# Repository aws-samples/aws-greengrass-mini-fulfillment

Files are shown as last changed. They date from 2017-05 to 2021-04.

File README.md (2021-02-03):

## The Greengrass mini-fulfillment center example 

At re:Invent 2016 AWS Greengrass was introduced to the world. This miniature 
fulfillment center demonstration was used to display what could be done with 
Greengrass when announced. It has since been upgraded to use the publicly available 
version of [Greengrass](https://aws.amazon.com/greengrass/) v1.
 
A [video](https://youtu.be/XQQjX8GTEko?t=27m27s) was taken of the completed and 
operational Greengrass-based miniature fulfillment center, a.k.a. "dual robot arm demo" 
in action at re:Invent. Since re:Invent this demo and example has continued to 
evolve. It has been the seed for [other demos](https://youtu.be/dpatdO2uPCA) and 
now supports Greengrass [discovery](http://docs.aws.amazon.com/greengrass/latest/developerguide/gg-discover-api.html) 
capabilities. 

The artifacts, example code, and instructions to construct this demo are 
available in this repository as an example. We look forward to seeing what 
you'll do with it.

#### Directory Structure and Noteworthy Files
```
aws-greengrass-mini-fulfillment/
  +- docs/
  |  +- BOM.md         -- the bill of materials necessary for construction
  |  +- CONSTR.md      -- instructions for physical construction (TODO)
  |  +- INSTALL.md     -- instructions for software provisioning and install
  |  +- OPERATE.md     -- instructions for operation of the demo
  |  +- TIDBITS.md     -- tiny pieces of setup information that might be helpful
  |  +- TROUBLE.md     -- troubleshooting of install and operation
  |
  +- groups/
  |  +- cert_setup.py  -- generates local certificates used by Greengrass groups 
  |  +- group_setup.py -- provisions and deploys example Greengrass groups 
  |  +- servo_setup.py -- prepares the servo communication code for example use  
  |  |
  |  +- arm/           -- the code and config necessary for an arm host
  |  |  +- ggd/        -- the Greengrass Devices that will be run on the Host
  |  |  |  +- servo/   -- the servo communications libraries 
  |  |  +- inv_arm/    -- the specific config and certs for the `inv_arm` group 
  |  |  +- sort_arm/   -- the specific config and certs for the `sort_arm` group
  |  | 
  |  +- lambda/        -- the Lambda functions used in the Greengrass groups
  |  |
  |  +- master/        -- the directory of the `master` Greengrass group 
  |     +- certs/      -- the group AWS IoT and local certs to be copied to Core
  |     +- ggd/        -- the Greengrass Devices that will be run on the Host
  |        +- certs/   -- the client certs used by GG devices
  |        +- flask/   -- where the web GG device gets files to serve
  |        +- servo/   -- the servo communications libraries 
  |
  +- models/           -- the models used to 3D print components of this demo
  +- LICENSE
  +- README.md -- this file
  +- requirements.txt
```

After following the [installation instructions](docs/INSTALL.md), each directory 
contains all the files necessary to support one of the three Demo groups' hosts. 
There are three Greengrass Groups named: 

| Group | Host Name | Description |
| :---: | :---: | :--- |
| `inv_arm` | `inv_arm-pi` | contains the Inventory Arm devices and the Inventory Arm Core |
| `master` | `master-pi` | contains both the Conveyor Belt devices and the Master Core |
| `sort_arm` | `sort_arm-pi` | contains the Sorting Arm devices and the Sort Arm Core |

The demo behavior is broken into the concept of a series of simple control stages 
organized by Group. Those stages are:

| Group | Control Stages |
| :--- | :--- |
| **Inventory Arm** | `... > Home > Finding > Pickup > Shipping > Home > ...` |
| **Master** | `..conveyor direction..` |
| **Sorting Arm** | `... > Home > Finding > Pickup > Sorting > Home > ...` |

As shown in the video above, even with these simple stages the interaction between 
the three Groups displays complex, cohesive, and coordinated behaviors.

This is possible because the whole system is modeled as a collection of micro-services. 
Those micro-services then leverage high-speed local messaging to enable communication 
within and between groups, as well as transactional state control using local device 
shadows. 

The high-level, local architecture of the demo is:
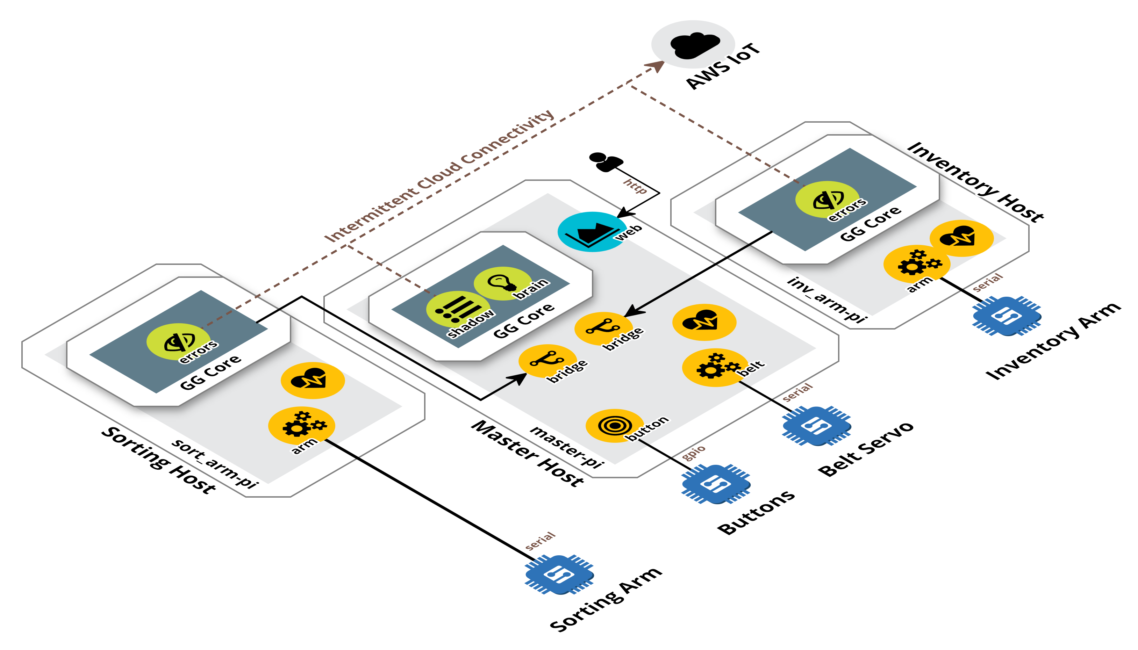
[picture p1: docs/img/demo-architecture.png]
mini-fulfillment demo architecture


#### Master/Conveyor Host
There are six processes on this host:
- the Master Greengrass Core
- the [`heartbeat`](groups/master/ggd/heartbeat.py) Greengrass Device (GGD) process
- the [`bridge`](groups/master/ggd/bridge.py) GGD process
- the [`belt`](groups/master/ggd/belt.py) GGD process -- manages the conveyor belt servo
- the [`button`](groups/master/ggd/button.py) GGD process -- manages the button box's red, green, and white control buttons
- the [`web`](groups/master/ggd/web.py) GGD process

Within the Master Core, these are the Lambda functions:
- [`MasterErrorDetector`](groups/lambda/MasterErrorDetector/error_detector.py) -- this function monitors local telemetry and detects any error states
- [`MasterBrain`](groups/lambda/MasterBrain/master_brain.py) -- this function monitors the fabric of telemetry coming from the 
  bridges and the local GGDs. This function will decide what to do with respect 
  to current telemetry and errors in the system

There is a web visualization on this host. If one browses to: `<master_ip>:5000` a 
visualization that reads data from the Master Core can be seen. 

#### Inventory Arm Host
There are three processes on this host:
- the Inventory Arm Greengrass Core
- the [`heartbeat`](groups/arm/ggd/heartbeat.py) Greengrass Device (GGD) process
- the [`arm`](groups/arm/ggd/arm.py) GGD process

Within the Inventory Arm Core, this is the Lambda function:
- [`ArmErrorDetector`](groups/lambda/ArmErrorDetector/error_detector.py) -- this function monitors local telemetry and detects any error states

#### Sorting Arm Host
There are three processes on this host:
- the Sorting Arm Greengrass Core
- the [`heartbeat`](groups/arm/ggd/heartbeat.py) Greengrass Device (GGD) process
- the [`arm`](groups/arm/ggd/arm.py) GGD process

Within the Sort Arm Core, this is the Lambda function:
- [`ArmErrorDetector`](groups/lambda/ArmErrorDetector/error_detector.py) -- this function monitors local telemetry and detects any error states

#### Noteworthy Files
There are some noteworthy files in the repository that centralize a fair amount 
of work around the instantiation of this demonstration.
- `groups/group_setup.py` – performs all provisioning of each host's Greengrass Group. 
This file has commands that are useful when instantiating this demo and that demonstrate the use of the Greengrass REST APIs.
    - `create <group_type> <config_file>` – creates a Greengrass Group for a given 
    group type and configuration file. Also stores all of the provisioning 
    artifacts (i.e. `GroupID`, `CoreDefinitionId`, etc.) in the local configuration file.
    - `deploy <config_file>` – deploys a previously provisioned Greengrass Group
    - `clean-all <config_file>` – cleans up the entirety of a Greengrass Group 
    and the locally stored provisioning artifacts.
- `groups/servo_setup.py` – prepares the servo manufacturer's communication library 
for use on a Raspberry Pi with the Raspbian OS.

## DIY
If you'd like to build a copy of this demo yourself you'll want to read both 
the [installation instructions](docs/INSTALL.md) and the 
[construction instructions](docs/CONSTR.md). Please share any feedback you have 
or questions you run into here as [Issues](https://github.com/awslabs/aws-greengrass-mini-fulfillment/issues).

## Special Thanks
[Brett Francis](https://github.com/brettf) and [Todd Varland](https://github.com/toddvarland) would like to thank the following. Without their 
help and existence we simply would not have made this demo.

> **The Francis Family, The Varland Family, [gg-group-setup](https://github.com/awslabs/aws-greengrass-group-setup), 
[ROBOTIS](https://github.com/ROBOTIS-GIT/DynamixelSDK), [Servode](https://github.com/brettf/servode), 
Pretty Lights, Sigur Ros, Flume - Insanity, Amazon.com, HBO Silicon Valley, The [Greengrass](https://aws.amazon.com/greengrass/) Developers**

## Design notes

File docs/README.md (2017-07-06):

#### ToC

| File | Description |
| :--- | :--- |
| `BOM.md` | the bill of materials necessary for construction|
| `CONSTR.md` | instructions for physical construction |
| `INSTALL.md` | instructions for software installation and example provisioning |
| `OPERATE.md` | instructions for operation of the example |
| `TIDBITS.md` | tiny pieces of setup information that might be helpful |
| `TROUBLE.md` | troubleshooting of install and operation |

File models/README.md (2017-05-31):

The 3d printing files for the robot arms.

`TODO: assembly instructions`

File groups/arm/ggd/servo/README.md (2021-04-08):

# Servode
An ode to Python code that uses Servos ([ROBOTIS](https://github.com/ROBOTIS-GIT/DynamixelSDK) first)

## Usage
### As a library
When using Servode as a library use a single ServoProtocol instance per 
connected servo bus. One ServoProtocol can be shared across threads.

To connect a Servo and read a register (example: `present_position`):
```python
with ServoProtocol() as sp:
    servo = Servo(sp=sp, servo_id=1)
    # to read a value
    value = servo['present_position']
```

To connect a Servo and write a register (example: `goal_position`):
```python
with ServoProtocol() as sp:
    servo = Servo(sp=sp, servo_id=1)
    # to read a value
    servo['goal_position'] = 128
```

To connect a group of servos and write values to a register (example: `goal_position`):
```python
with ServoProtocol() as sp:
    sg = ServoGroup()
    sg['base'] = Servo(sp, 10)
    sg['elbow'] = Servo(sp, 11)
    sg['wrist'] = Servo(sp, 12),
    sg['claw'] = Servo(sp, 13)

   sg.write("goal_position", [
        100,  # first servo value
        200,  # second servo value
        330,  # third servo value
        400   # fourth servo value
    ])
```

### From the command-line
To read a register from one servo:
```
$ ./servode.py read_register --sid 10
2016-11-04 06:01:42,582|servode |INFO: Read register: 'present_position'
2016-11-04 06:01:42,587|servode |INFO: Servo:10 value:497
```
To read a register from two servos:
```
$ ./servode.py read_register --sid 10 --sid 11
2016-11-04 06:01:42,582|servode |INFO: Read register: 'present_position'
2016-11-04 06:01:42,587|servode |INFO: Servo:10 value:497
2016-11-04 06:01:42,589|servode |INFO: Servo:11 value:102
```
To write a value to a register on one servo:
```
$ ./servode.py write_register goal_position 490 --sid 10
2016-11-04 06:23:28,716|servode |INFO: Servo:10 wrote value:490 to register:goal_position
```
To write a value to a register on two servos:
```
$ ./servode.py write_register goal_position 490 --sid 10 --sid 11
2016-11-04 06:24:11,614|servode |INFO: Servo:10 wrote value:490 to register:goal_position
2016-11-04 06:24:11,616|servode |INFO: Servo:11 wrote value:490 to register:goal_position
```
## Installation

1. Download the latest [ROBOTIS SDK](https://github.com/ROBOTIS-GIT/DynamixelSDK/releases)
2. Change to the directory where `servode.py` resides
3. Un-tar the ROBOTIS SDK:

    ```
    #example
    tar -xvf ~/download/dir/of/DynamixelSDK-#.#.#.tar
    ```  
4. Copy the dynamixel python functions to the directory where `servode.py` resides

    ```
    # example
    cp DynamixelSDK-#.#.#.tar/python/dynamixel_functions_py/dynamixel_functions.py .
     ```
5. Edit `dynamixel_functions.py` to use the CDLL for your OS. 
    - Example CDLL edit for Raspbian Jessie: 
    ```python
        ...snip...
        from ctypes import cdll
        # dxl_lib = cdll.LoadLibrary("../../c/build/win32/output/dxl_x86_c.dll") # for windows 32bit
        # dxl_lib = cdll.LoadLibrary("../../c/build/win64/output/dxl_x64_c.dll") # for windows 64bit
        # dxl_lib = cdll.LoadLibrary("../../c/build/linux32/libdxl_x86_c.so")    # for linux 32bit
        # dxl_lib = cdll.LoadLibrary("../../c/build/linux64/libdxl_x64_c.so")    # for linux 64bit
        dxl_lib = cdll.LoadLibrary("DynamixelSDK-3.4.1/c/build/linux_sbc/libdxl_sbc_c.so")    # for linux 32bit sbc
        ...snip...

    ```

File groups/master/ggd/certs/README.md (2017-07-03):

All the Greengrass Device specific certificates and keys land here

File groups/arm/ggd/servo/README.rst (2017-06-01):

Servode
=======
An ode to Python code that uses Servos (ROBOTIS first)

`Getting Started <https://github.com/brettf/servode>`_

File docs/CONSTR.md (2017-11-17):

# AWS Mini Fulfillment Center Construction

Welcome to the AWS Mini Fulfillment Construction Documentation. 

## Construction Instructions

Overall the process is:
1) acquire parts from the [Bill of Materials](BOM.md)
1) print 3D parts
1) assemble each [arm](#the-arm)
1) assemble [control box](#the-control-box)
1) assemble [conveyor](#the-conveyor)
1) follow [software installation](INSTALL.md)
1) push green button

## The Arm
The quickest way to assemble the various parts that form a complete robot arm is 
to assemble them in four separate sections and combine them at the intersection 
points. The arm's four main sections are in this image:

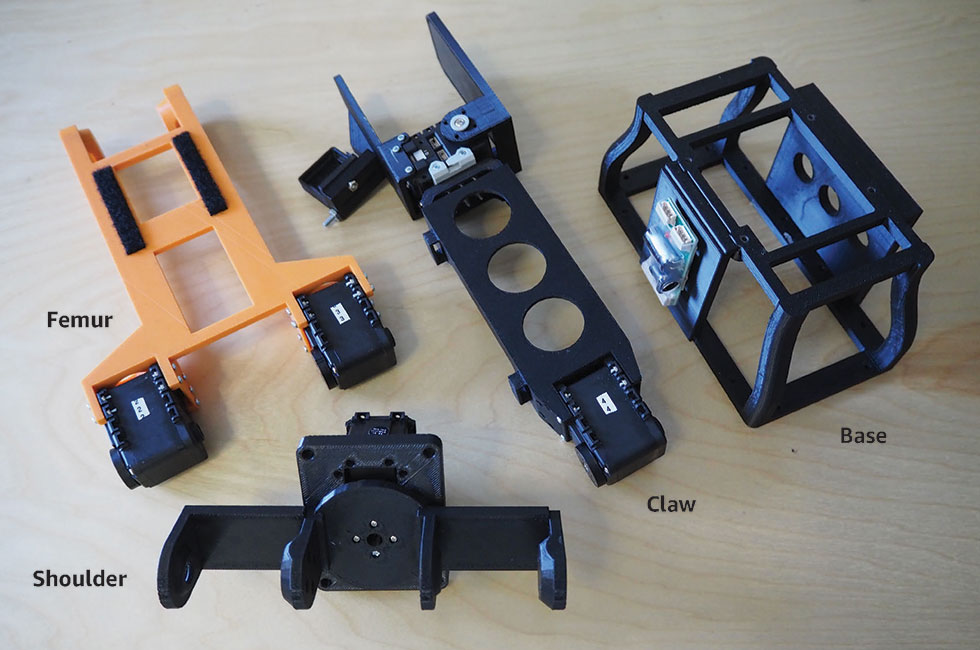
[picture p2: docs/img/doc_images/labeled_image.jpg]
four main parts


### The Shoulder

| Image | Instructions | 
| :--- | :--- |
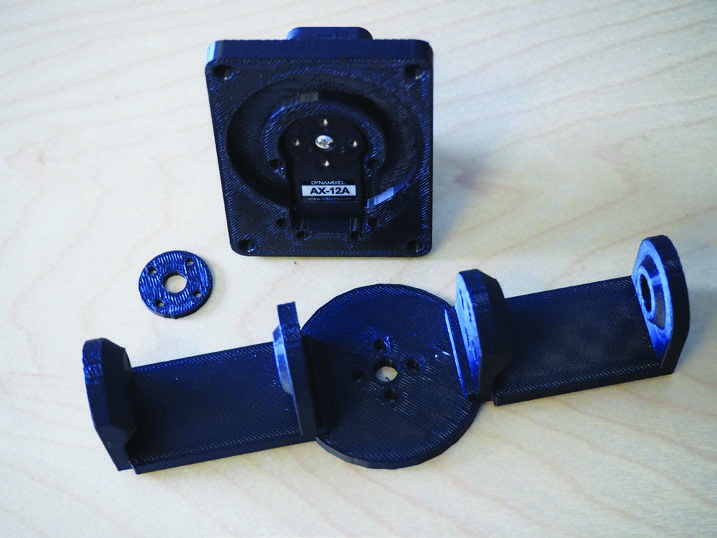
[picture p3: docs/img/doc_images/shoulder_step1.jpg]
|  | Connect the Servo to the large square spacer using six N1 bolts and six S3 screws. |
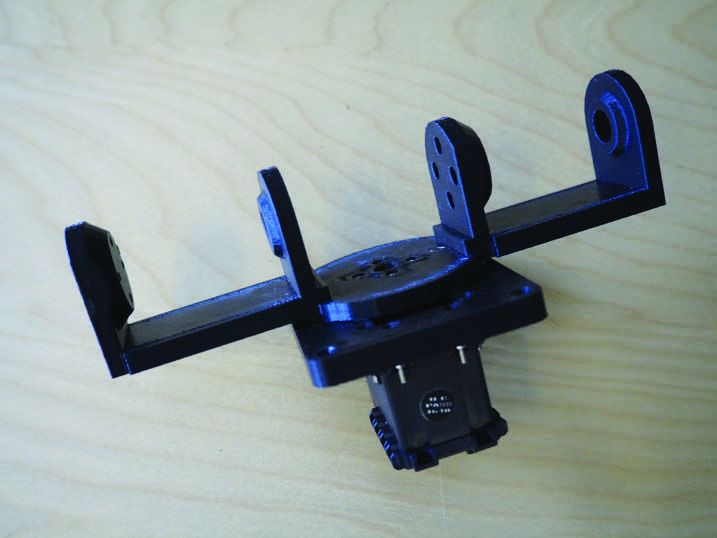
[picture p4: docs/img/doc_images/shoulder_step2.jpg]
|  | Attach the shoulder piece to the servo fly-wheel. Make sure to include the small spacer between the fly-wheel and shoulder piece. |
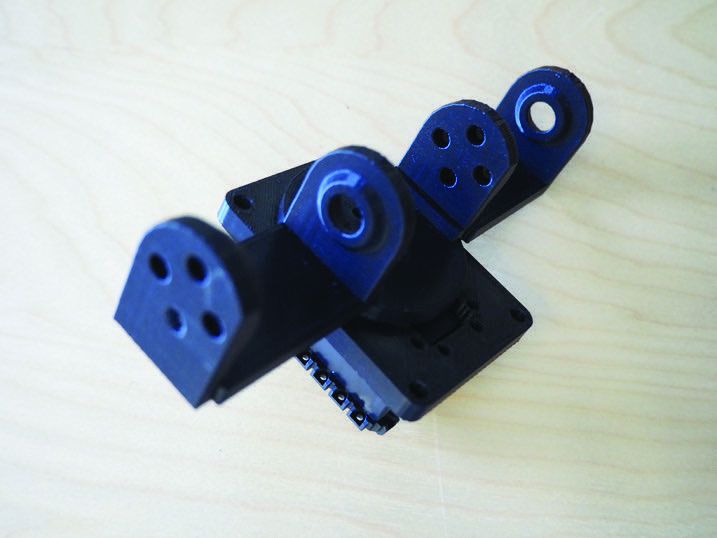
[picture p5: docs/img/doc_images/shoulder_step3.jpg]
|  | When you have completed it, the shoulder should be pointing so that the four holes are on the left side. |

### The Claw

| Image | Instructions | 
| :--- | :--- |
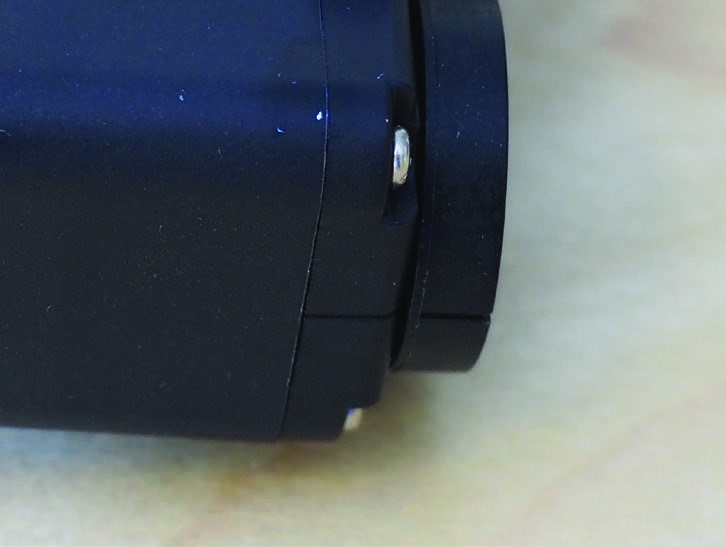
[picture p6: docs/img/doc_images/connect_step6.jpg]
|  | In general, when connecting a servo to any other part, start with the fly-wheel in the initial state, indicated by the aligned lines in the plastic. |
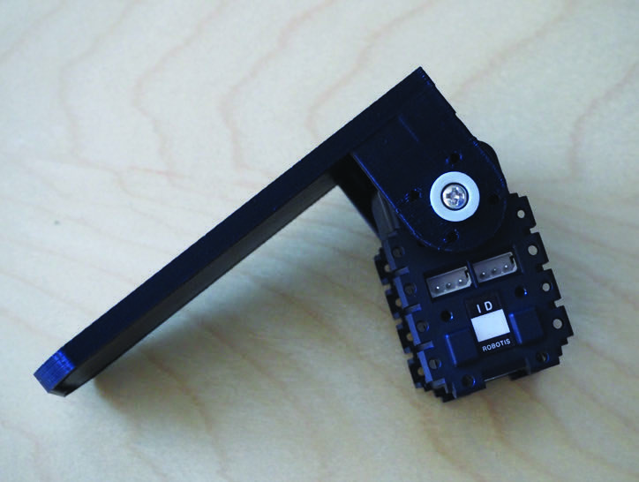
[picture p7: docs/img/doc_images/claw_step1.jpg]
|  | Position the servo fly-wheel so that it is pointing downward and use four S3 screws to connect the right clamp to the fly-wheel. |
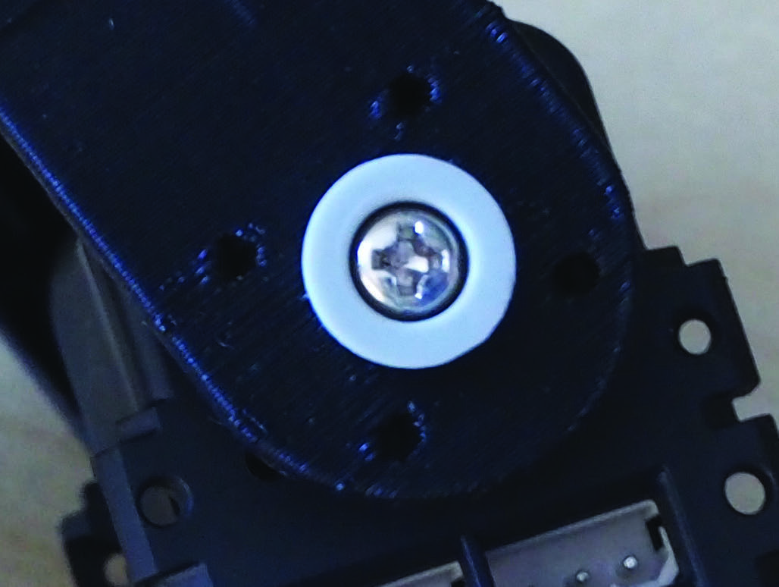
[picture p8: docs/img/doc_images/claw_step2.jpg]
|  | On the top side, you’ll need to insert the BU washer through the center hole on the clamp and fasten it to the servo using an S4 screw. |
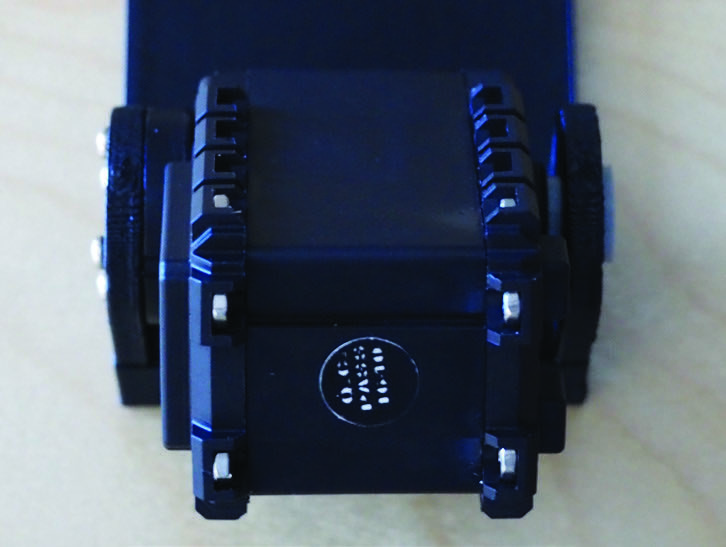
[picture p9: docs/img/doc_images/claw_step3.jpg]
|  | Position the Tibia assembly like shown so that the fly-wheel is pointing to the left and pre-insert six N1 bolts as shown. |
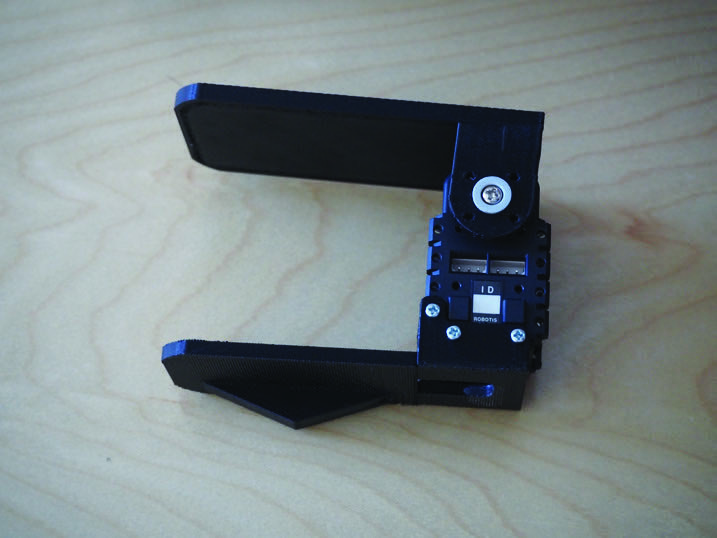
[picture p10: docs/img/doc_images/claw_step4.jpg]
|  | Return the assembly to the original position and attach the left clamp to the servo using six S3 screws. Be sure the N1 bolts line up. |
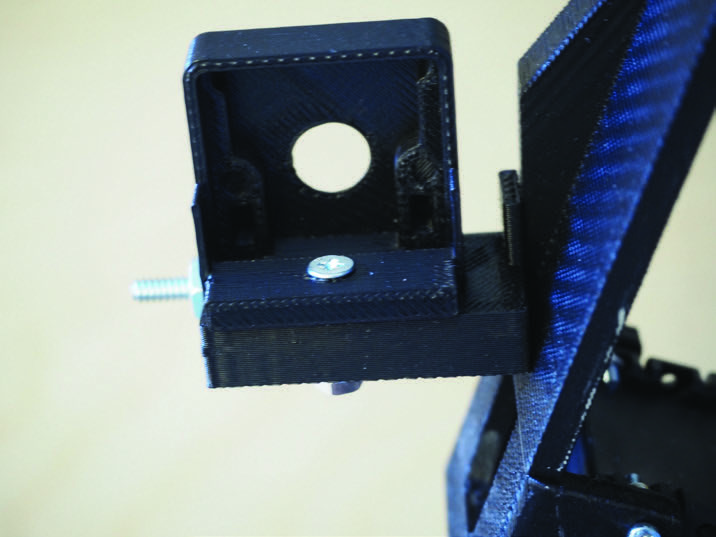
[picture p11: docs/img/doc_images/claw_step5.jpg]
|  | Attach the two camera housing pieces together using an `N` nut and S3 screw. |
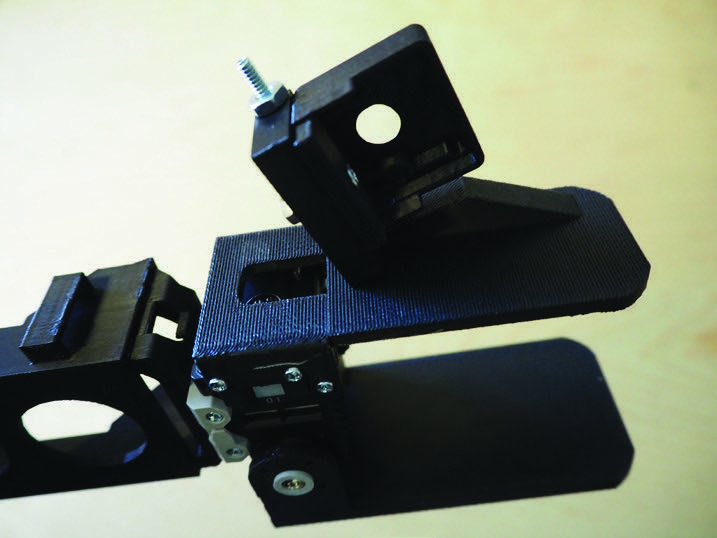
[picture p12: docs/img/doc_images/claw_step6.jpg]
|  | Then, use any 2” long screw and bolt to attach the camera housing to the left clamp. |
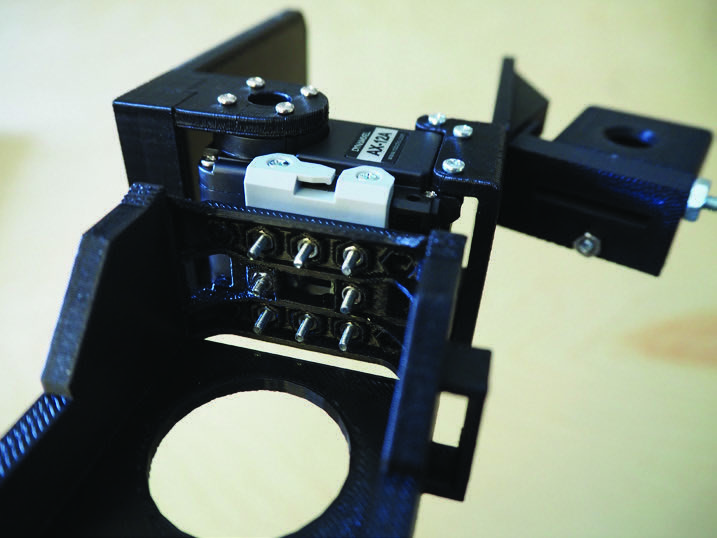
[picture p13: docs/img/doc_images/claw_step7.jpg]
|  | Place eight N1 bolts into the slotted holes at the flat end of the Tibia and fasten the FP servo mount using eight S3 screws. |
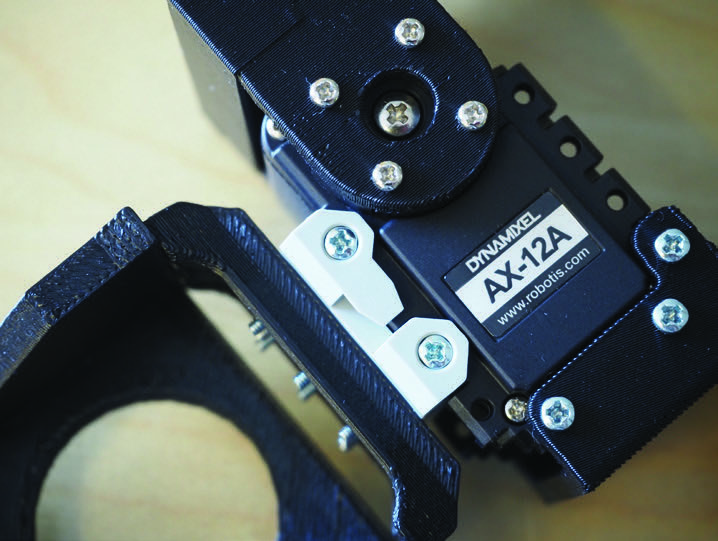
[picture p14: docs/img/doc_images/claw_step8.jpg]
|  | Attach the Claw to the `FP04` mount as shown in this photo. Remember to place four N1 bolts into the servo slots accordingly and fasten  with S3 screws. |
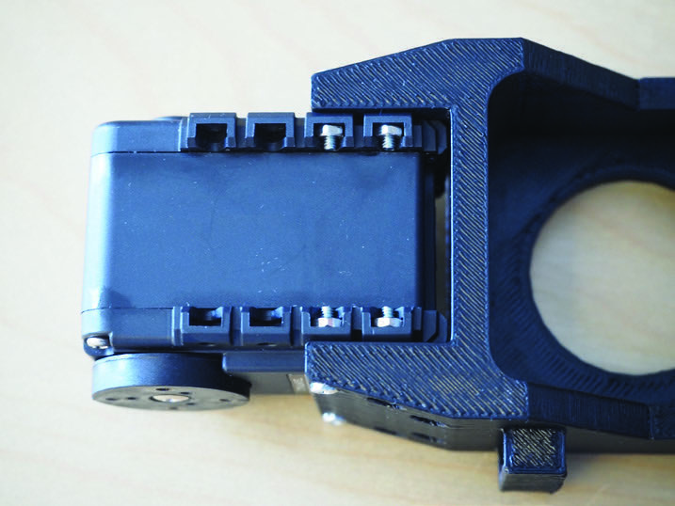
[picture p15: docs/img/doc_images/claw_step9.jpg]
|  | Position the servo at the bottom end of the Tibia as shown so the fly-wheel faces the side with the cable slots. Insert twelve N1 bolts into the servo and fasten with S3 screws. |

### The Femur

| Image | Instructions | 
| :--- | :--- |
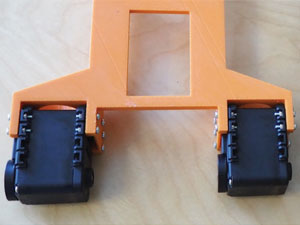
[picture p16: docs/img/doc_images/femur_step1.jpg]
|  | Begin the Femur assembly by placing the the piece so that the flat side with the rectangular cut-outs are on top. The servo fly-wheels should be pointing to the left. |
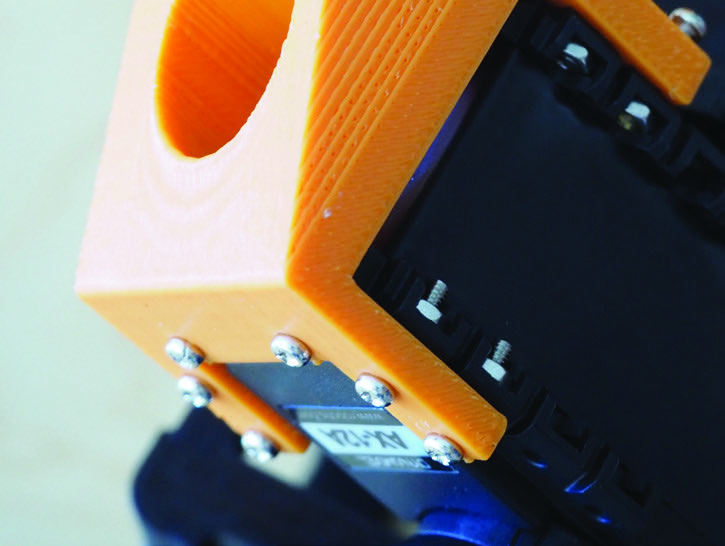
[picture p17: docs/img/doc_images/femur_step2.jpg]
|  | Each servo will be connected to the Femur using six S3 screws on the outer side and five on the inner side. Be sure to pre-insert the N1 bolts into the corresponding servo slot. |
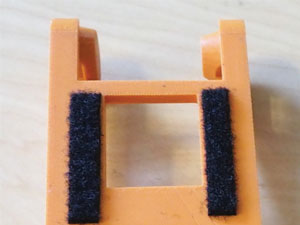
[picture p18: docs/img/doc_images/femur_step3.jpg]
|  | Attach two strips of velcro for the Raspberry Pi to mount onto the Femur. |

### The Base

| Image | Instructions | 
| :--- | :--- |
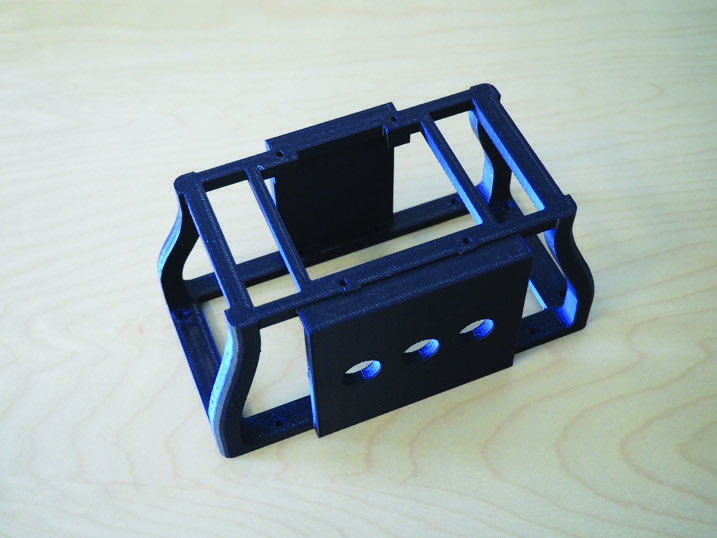
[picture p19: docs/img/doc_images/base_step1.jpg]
|  | The base’s front side is marked by the 3 holes, and the back with the flat side. The base will contain a power converter that is attached with velcro. |
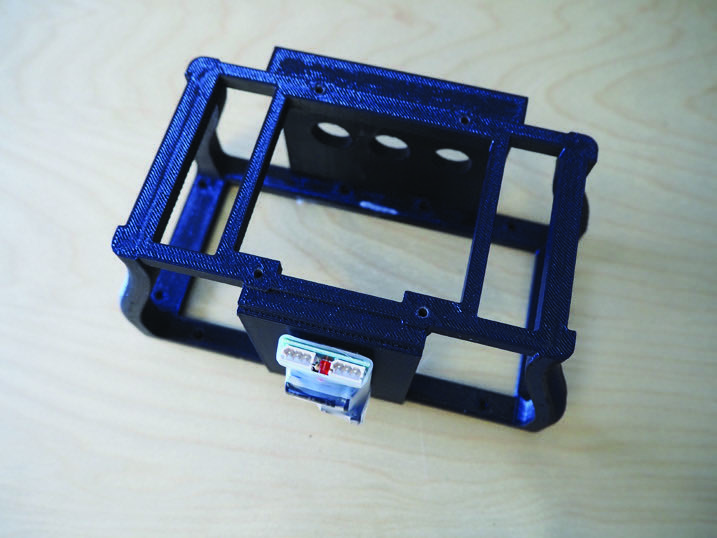
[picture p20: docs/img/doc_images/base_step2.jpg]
|  | Attach the `SMPS2DYNAMIXEL` power converter mounted to the back with the three pins facing up. *Note: there are both three pins and four pins on the power converter.* |
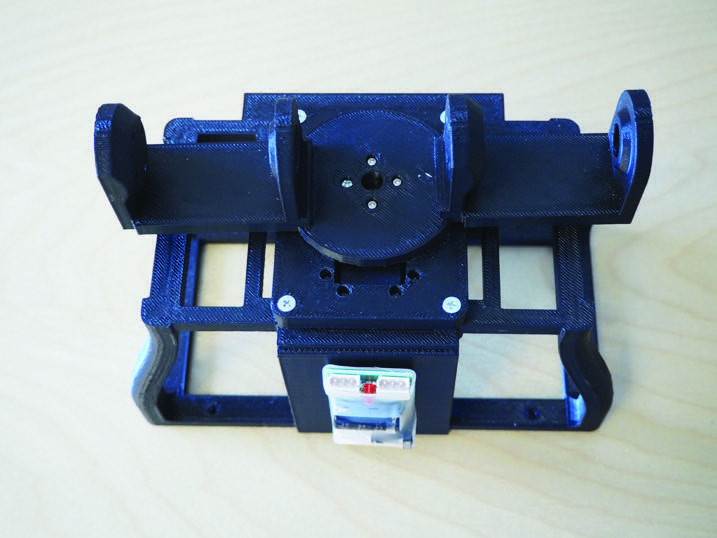
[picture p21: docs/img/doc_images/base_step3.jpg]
|  | Using four M3x16mm Flat head screws (equal to SB screws but flat head), mount the shoulder assembly to the base. Flat heads are essential or the shoulder's rotation will be blocked. |

### Connect at the Joints

| Image | Instructions | 
| :--- | :--- |
|  | In general, when connecting a servo to any other part, start with the fly-wheel in the initial state, indicated by the aligned lines in the plastic. |
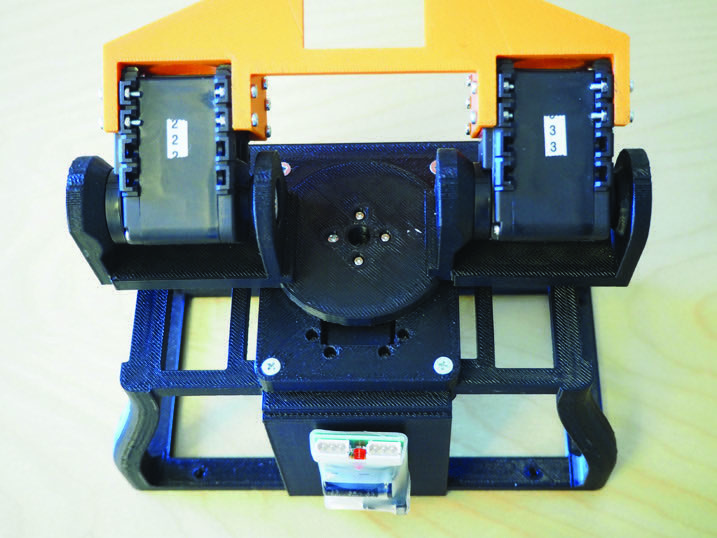
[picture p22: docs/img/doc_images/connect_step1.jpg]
|  | Attach the Femur assembly to the Shoulder/Base with the fly-wheel on the servo facing to the left with S3 screws. Use BU-WA washers and an SB screw to fasten the other end of the servo. |
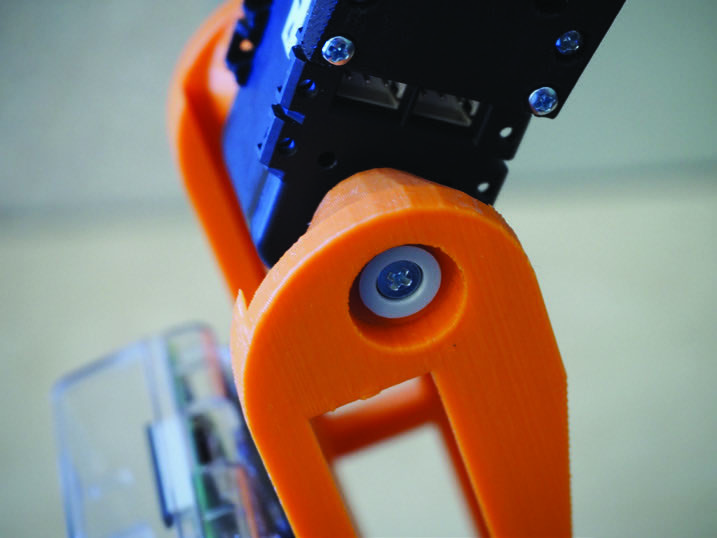
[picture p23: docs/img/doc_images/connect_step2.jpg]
|  | Use one BU-WA washer and SB screw to attach the bottom (or right side when viewing the arm from the back). |
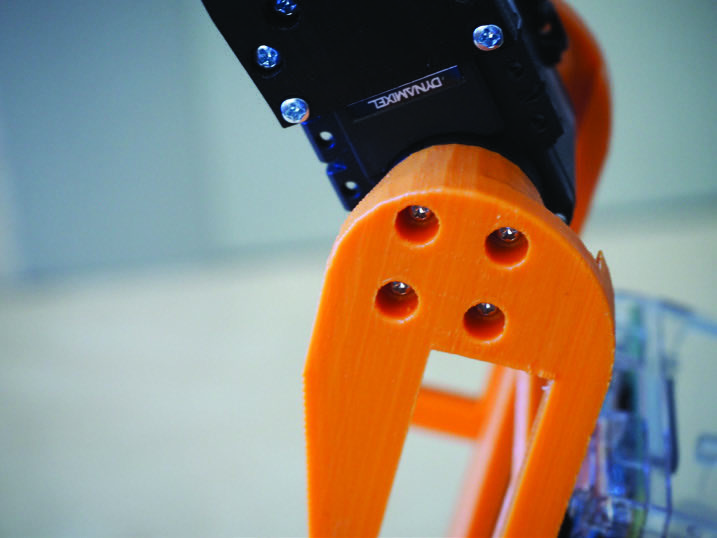
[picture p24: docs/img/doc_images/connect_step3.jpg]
|  | Use four S4 screws to fasten the Claw assembly to the Femur assembly. *Note: the S4 screws are needed due to the extra thickness of the Femur.* |
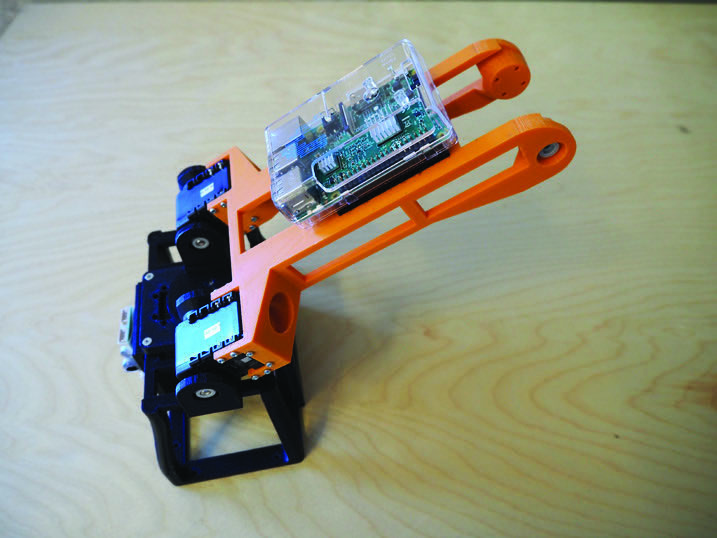
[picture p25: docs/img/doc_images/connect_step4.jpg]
|  | Attach the Raspberry Pi to the Femur using the velcro strips. |
|  | When attaching the Claw to the Femur, ensure the direction of the claw is as shown. |

### Cables and Power

| Image | Instructions | 
| :--- | :--- |
|  | The servos are daisy-chained using the 3P 200mm Robot Cable. Follow the images and connect as shown. |
|  | The cable will usually connect the previous servo on the left, and daisy chain out from the right slot. |
|  | Between the Elbow servo and Shoulder, you’ll need to splice a longer (by 3”) cable. |
|  | From the Elbow, connect to the right servo on the left (`in`) slot and connect the right (`out`) slot to the servo on the left. |
|  | From the right slot, connect to the bottom servo on the left slot. The left servo must be the one connected to the bottom. |
|  | The last servo in the daisy chain will connect to the the left servo using the left pin slot. Using the right pin slot connect to the power adapter. |
|  | The power adapter receives the bottom servo connection in the left slot and goes to the serial adapter from the right slot. |
|  | There is only one three pin slot on the serial adapter that is connected to the USB port on the Raspberry Pi. |
|  | Note that the switch must be in the up position if using the three pin slot. |

## The Control Box
    <TBD>

## The Conveyor
    <TBD>

> Note: The conveyor used in this example was inspired by [this fine work](http://www.instructables.com/id/DIY-Conveyor-belt/).

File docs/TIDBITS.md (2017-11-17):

### GG Tidbits

#### Enable GPIO on Raspberry Pi
Add the following to `/boot/config.txt` in order to enable GPIO on Jessie. 
```
# Enabled GPIO  
enable_uart=1
```
..and this:
```
max_usb_current=1
```
...to provide MAX power to the USB ports

#### Provision USB on Raspberry Pi for optimal use by USB2Dynamixel
Add this to the `/boot/cmdline.txt`
```
dwc_otg.speed=1
```
To limit USB speed to full speed 12Mbps (USB 1.1).

#### Install `screen` on each Raspberry Pi
Execute the command: `sudo apt-get install screen`
Then to run screen with a bash shell: `screen bash`

### Install Dependencies
```bash
sudo apt-get install python-devel
```
..and then using `pip` install:
```bash
sudo pip install -r requirements.txt
```

### Physical Setup
The conveyor should be 14" away from the arm base. 

### Checking Servode comms on a Host
```bash
cd ~/mini-fulfillment/groups/arm/ggd
python -m servo.servode ping [servo_id]
```

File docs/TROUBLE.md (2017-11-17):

## Troubleshooting
#### An arm does not start
- If `arm.py` does not start, simply exits, or shows this error:
```
 SE:[Errno 111] Connection refused
Traceback (most recent call last):
  File "./arm.py", line 324, in <module>
    initialize()
  File "./arm.py", line 76, in initialize
    raise EnvironmentError("connection to GG Core MQTT failed.")
EnvironmentError: connection to GG Core MQTT failed.
```
...please ensure you have executed `sudo /greengrass/greengrassd start`.

#### Has everything stopped?
To ensure nothing is running you can execute the following and expect 
the subsequent output.
```
$ screen -ls
No Sockets found in /var/run/screen/S-pi.
```

#### IP addresses change
If the IP addresses change for some reason:
1. Do a Lan Scan to find the three Raspberry Pi 3's
2. Take note of each host's new IP
3. Update the files on each host to reflect the new IP addresses. Specifically:
```
~/mini-fulfillment/master/ggd/config.py
~/mini-fulfillment/inv_arm/ggd/config.py
~/mini-fulfillment/sort_arm/ggd/config.py
```

#### Getting errors when Creating Cores
If you're getting errors when executing any of the `create` group commands:
```
$ ./group_setup.py create sort_arm <config_file>
...
```
check that the `<config_file>` aka. `cfg.json` file being used for each host is in 
the original state. The original state will have empty values for: 
`group_arn`, `group_id`, `group_version`, `lambda_list_arn`, `membership_id`, and `membership_list_arn` 

If any of those values are not empty, the `create` function has been run previously. 
  
If you still want to execute the `create` function, prior to executing `create` remove the Group containing the particular host's Greengrass Core. To do this, 
browse to the Greengrass console and delete the Group.

#### Getting errors when a Greengrass Core is launched
If you're getting the following error when executing `$ sudo /greengrass/ggc/core/greengrassd start`
```
Setting up greengrass daemon
Validating execution environment
Found cgroup subsystem: cpu
Found cgroup subsystem: cpuacct
Found cgroup subsystem: blkio
Found cgroup subsystem: memory
Found cgroup subsystem: devices
Found cgroup subsystem: freezer
Found cgroup subsystem: net_cls

Starting greengrass daemon
Greengrass daemon 20301 failed to start
thing name is unresolved, error: Certificate hash not found in cores list. ThingName is unresolved
```
Then the Greengrass Core was used previously with a different Thing and Certificate. Either re-install the 
Greengrass Core software from scratch, or edit the `/greengrass/ggc/deployment/group/group.json` back to an unused state, as follows:
```json
{
    "Version": "test group version",
    "Devices": [],
    "Cores": [],
    "GroupDefinitions": {
        "Logging": {
            "Content": [
                {
                    "Component": "GreengrassSystem",
                    "Level": "DEBUG",
                    "Type": "FileSystem",
                    "Space": 128
                }
            ]
        },
        "Lambdas": {
            "ref": null,
            "Content": []
        },
        "Subscriptions": {
            "ref": null,
            "Content": []
        },
        "ShadowSync": {
            "ref": null,
            "Content": []
        }
    },
    "Region": null
}

```  
`-=-=-=-=-`

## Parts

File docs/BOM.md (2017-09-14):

## Bill of Materials

| Item | Quantity | Area | Source | Link |
| :--- | :---: | :---: | :---: | :---: |
| Raspberry Pi 3 Kit | 3 | arms, master | Amazon | [link](http://a.co/bFWXNNj) | 
| 32gb micro SD cards | 3 | arms, master | Amazon | [link](https://www.amazon.com/dp/B06XWN9Q99/ref=cm_sw_r_tw_dp_x_EohPzb09NQN4G) | 
| TP-Link N300 Wireless Wi-Fi Nano Travel Router | 1 | master | Amazon | [link](https://www.amazon.com/dp/B00TQEX8BO/ref=cm_sw_r_tw_dp_x_UQTSzb94MFQFX) | 
| 3D Printer Filament | 1kg | arms, master | Amazon | [link](http://a.co/bz9pbiy) | 
| Adafruit T-Cobbler Plus for Pi | 1 | master | Amazon | [link](https://www.amazon.com/dp/B00OG4X0DK/ref=cm_sw_r_tw_dp_x_MuhPzbYYWVD1N) | 
| Breadboard | 1 | master | Amazon | [link](https://www.amazon.com/dp/B071YQZDPZ/ref=cm_sw_r_tw_dp_x_zwhPzbJ77NZSZ) | 
| Neoprene mouse pad | 1 | arms | Amazon | [link](https://www.amazon.com/Quality-Selection-Comfortable-Mouse-Black/dp/B01J24K284/ref=sr_1_6) | 
| Raspberry Pi Camera | 2 | arms | Amazon | [link](https://www.amazon.com/dp/B01ER2SKFS/ref=cm_sw_r_tw_dp_x_.AhPzb94Q23DK) | 
| Ethernet Cables 5-foot | 3 | all | Amazon | [link](http://a.co/eXMoPUb) | 
| Ethernet Hub | 1 | all | Amazon | [link](http://a.co/7yoeQNY) | 
| Raspberr Pi camera cable 18" | 2 | arms | Amazon | [link](https://www.amazon.com/gp/product/B00QSJLWMW/ref=od_aui_detailpages00?ie=UTF8&psc=1) | 
| 4" zip ties | 1 | arms | Amazon | [link](https://www.amazon.com/dp/B01018DB2E/ref=cm_sw_r_tw_dp_x_eGhPzb0Y2XAFD) | 
| numbered wire markers | 1 | arms | Amazon | [link](https://www.amazon.com/dp/B007469OZK/ref=cm_sw_r_tw_dp_x_ALhPzbGSJA6X5) | 
| Contact cement | 1 | arms | Amazon | [link](https://www.amazon.com/dp/B000M2SKNU/ref=cm_sw_r_tw_dp_x_SMhPzbSCW1618) | 
| Dynamixel AX-12A Servos | 11 | arms, master | Robotis | [link](http://www.robotis.us/ax-12a/) | 
| Dynamixel USB2DYNAMIXEL_INT USB-to-Servo Adapter | 3 | arms, master | Robotis | [link](http://www.robotis.us/usb2dynamixel_int/) | 
| Dynamixel SMPS 110v Power | 3 | arms, master | Robotis | [link](http://www.robotis.us/smps-12v-5a-ps-10-us-110v/) | 
| Dynamixel SMPS2Dynamixel Serial Power Adapter | 3 | arms, master | Robotis | [link](http://www.robotis.us/smps2dynamixel/) | 
| Robotis S3 Bolt PHS M2 10 (50pcs) | 1 | arms, master | Robotis | [link](http://www.robotis.us/s3-bolt-phs-m2x10-50-pcs/) | 
| Robotis Robot Cable 3P 200mm (10pcs) | 3 | arms, master | Robotis | [link](http://www.robotis.us/robot-cable-3p-200mm-10pcs/) | 
| Robotis Bolt Nut Set BNS-10 | 1 | arms, master | Robotis | [link](http://www.robotis.us/bolt-nut-set-bns-10/) | 
| Robotis FP04-F3 (10pcs) | 1 | arms | Robotis | [link](http://www.robotis.us/fp04-f3-10pcs/) | 
| Red Momentary Button | 1 | master | Adafruit | [link](https://www.adafruit.com/products/1439) | 
| Green Momentary Button | 1 | master | Adafruit | [link](https://www.adafruit.com/product/1443) | 
| White Toggle Button | 1 | master | Adafruit | [link](https://www.adafruit.com/product/1479) | 
| Conveyor belt | 1 | conveyor | Seeedstudio | [link](https://www.seeedstudio.com/Conveyor-Belt-Kit-for-Dobot-Magician-p-2902.html) |

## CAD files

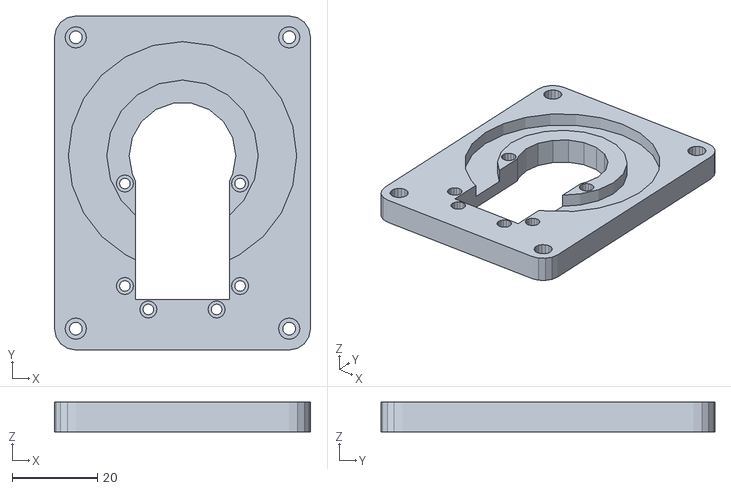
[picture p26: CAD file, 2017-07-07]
models/arm/gg_base_turn_table.stl
60.0 x 78.2 x 7.00

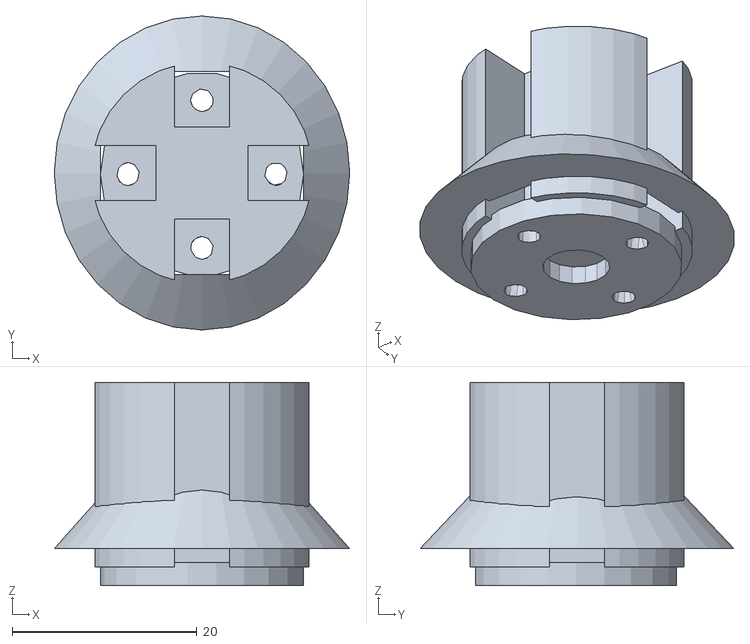
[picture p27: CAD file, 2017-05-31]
models/misc/gg_conveyor_gear_v2.stl
32.0 x 34.0 x 22.0

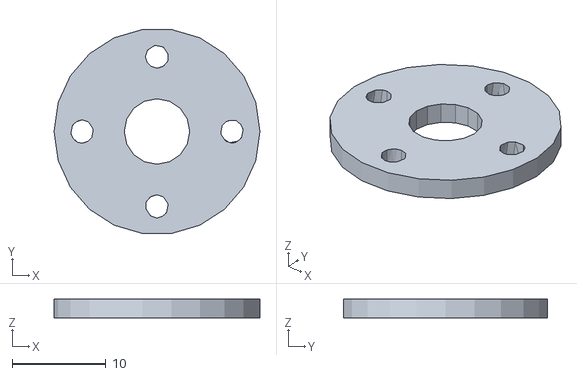
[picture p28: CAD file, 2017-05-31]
models/arm/gg_turret_spacer_2-0mm.stl
22.0 x 21.8 x 2.00

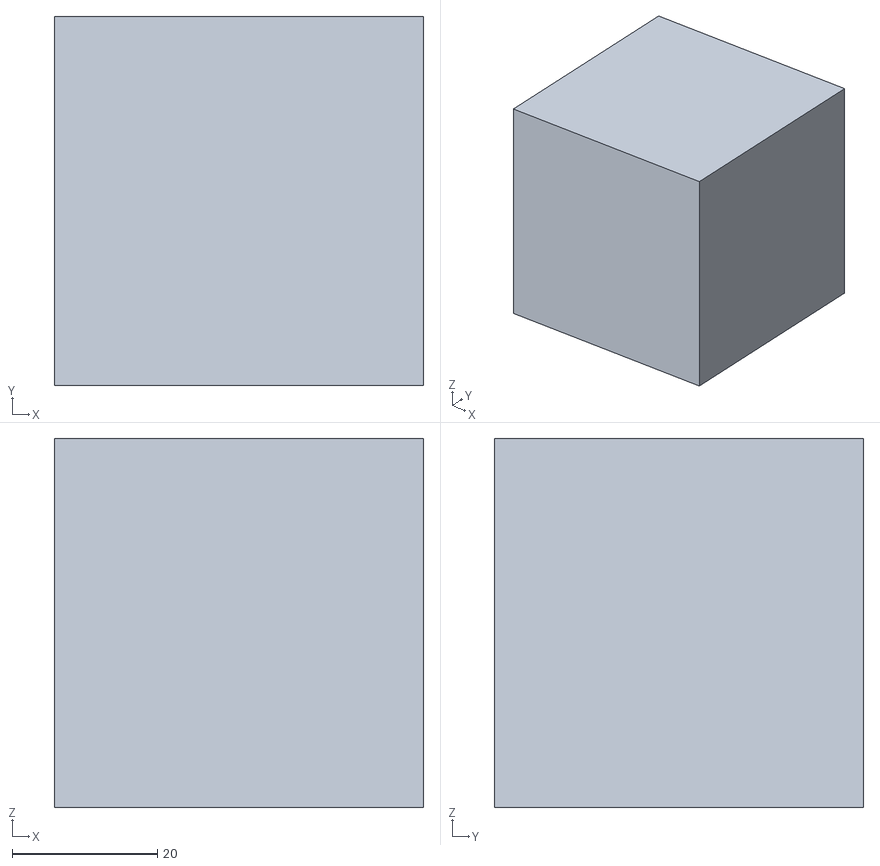
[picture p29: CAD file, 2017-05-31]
models/misc/gg_cube_2inch.stl
50.8 x 50.8 x 50.8

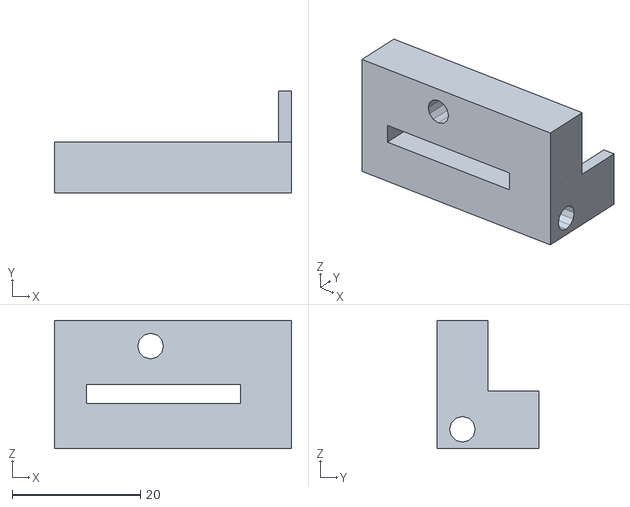
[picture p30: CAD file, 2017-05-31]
models/arm/gg_ef_cam_2_dof_v1-6.stl
37.0 x 16.0 x 20.0

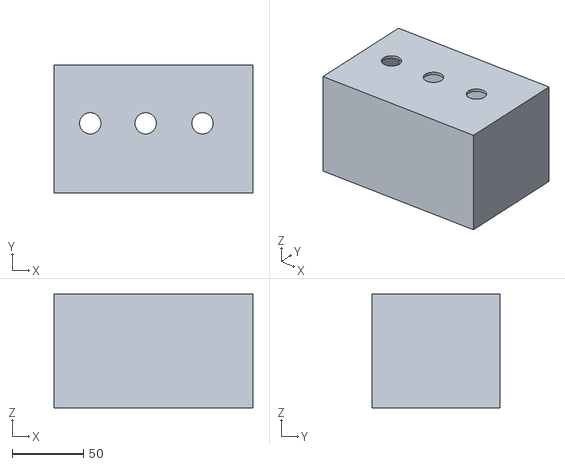
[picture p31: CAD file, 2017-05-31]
models/misc/gg_button_box.stl
140.0 x 90.0 x 80.0

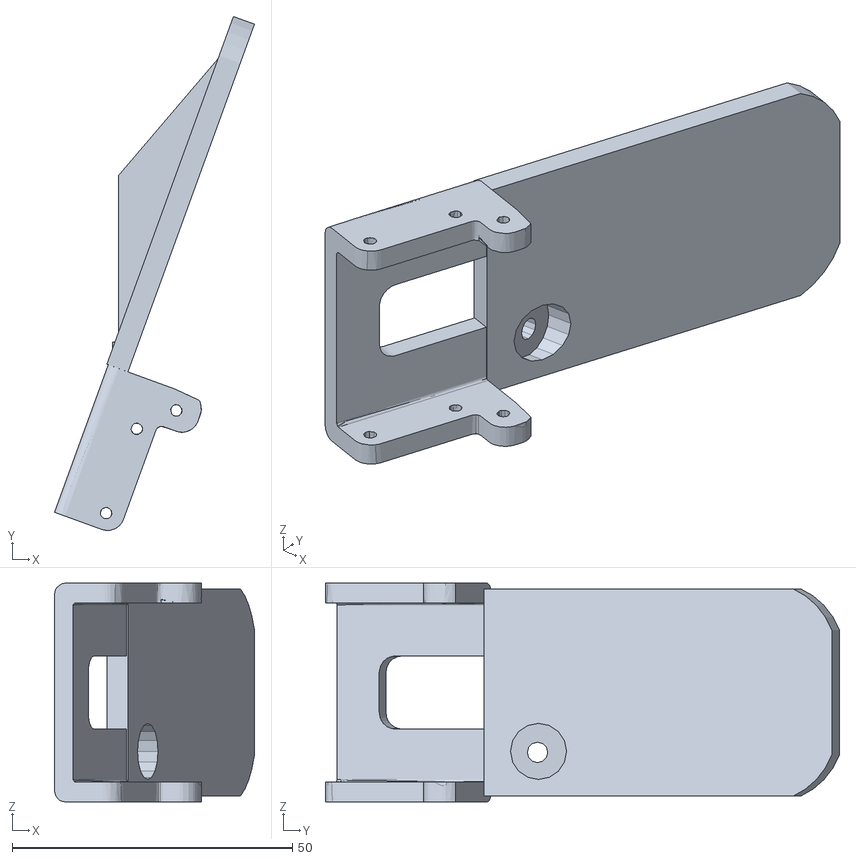
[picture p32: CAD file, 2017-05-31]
models/arm/gg_lower_ef_flex_cam_mount_v1.stl
35.7 x 91.7 x 39.0

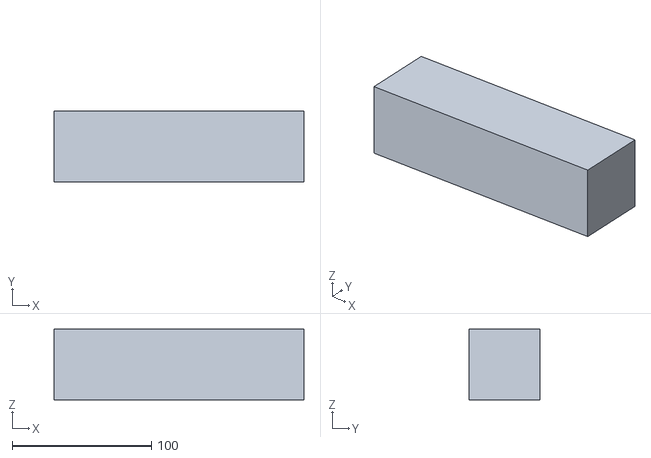
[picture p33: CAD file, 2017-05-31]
models/misc/gg_conveyor_stand.stl
179.5 x 50.8 x 50.8

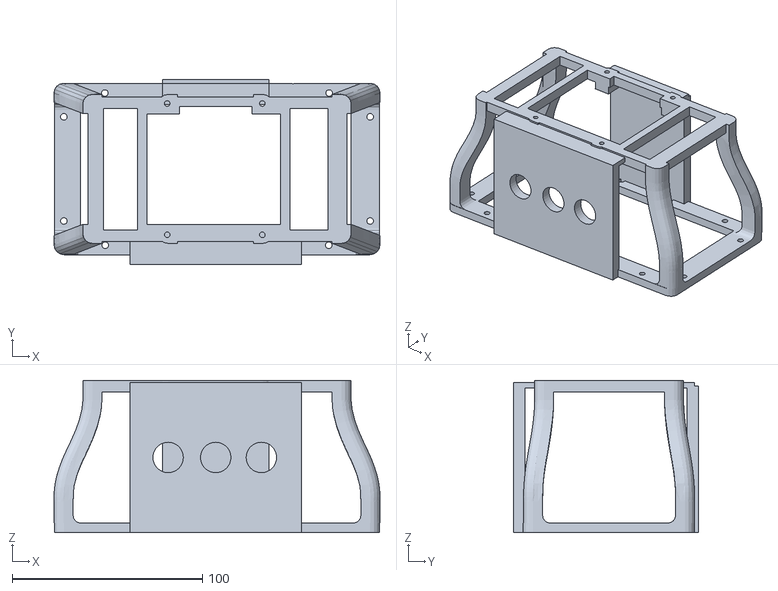
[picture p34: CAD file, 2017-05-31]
models/arm/gg_base_v2-3.stl
171.4 x 97.0 x 80.0

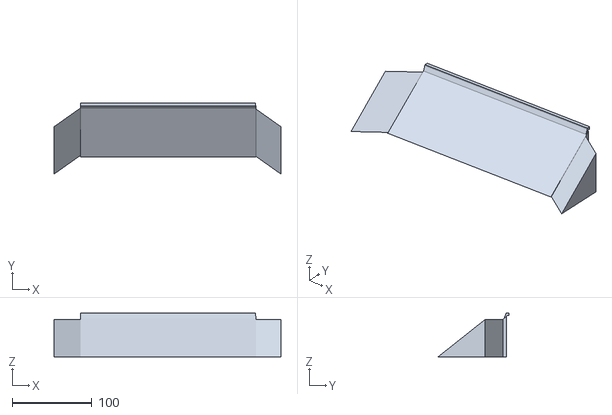
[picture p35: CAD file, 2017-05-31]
models/misc/gg_conveyor_kicker_v3.stl
284.0 x 89.1 x 55.0

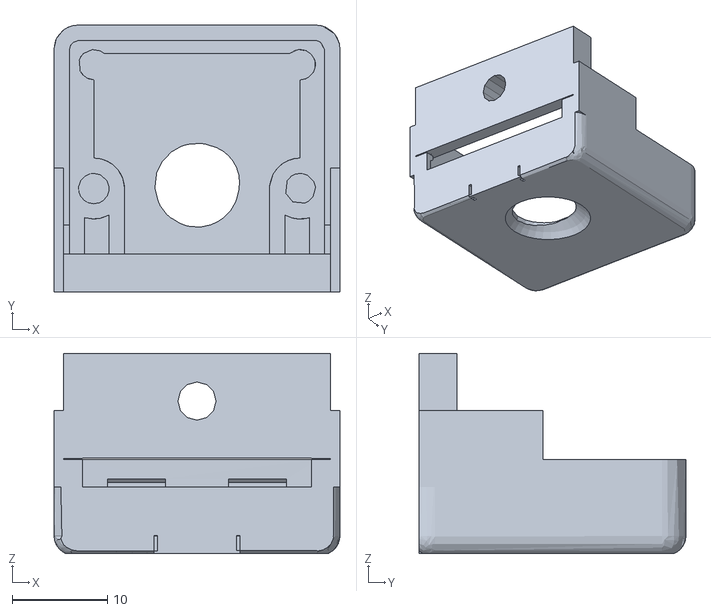
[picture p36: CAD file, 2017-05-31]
models/arm/gg_ef_cam_2_dof_v1-5.stl
30.0 x 28.0 x 21.0

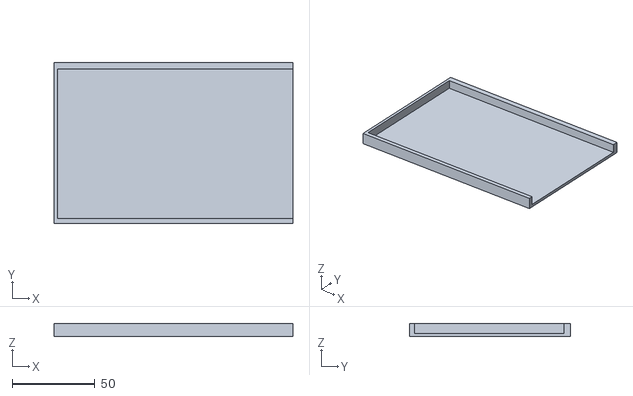
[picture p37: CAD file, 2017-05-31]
models/misc/gg_button_box_bottom.stl
144.0 x 97.0 x 8.00

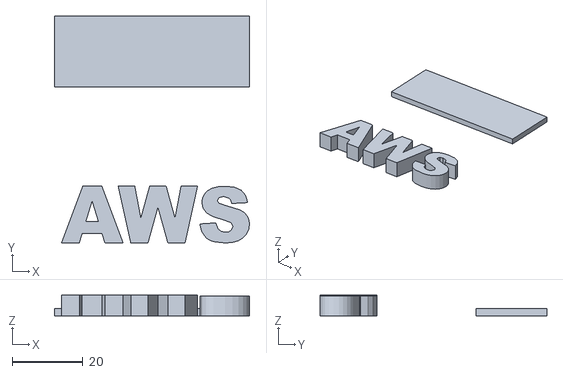
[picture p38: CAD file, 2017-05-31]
models/arm/gg_aws_logo.stl
55.0 x 64.0 x 5.79

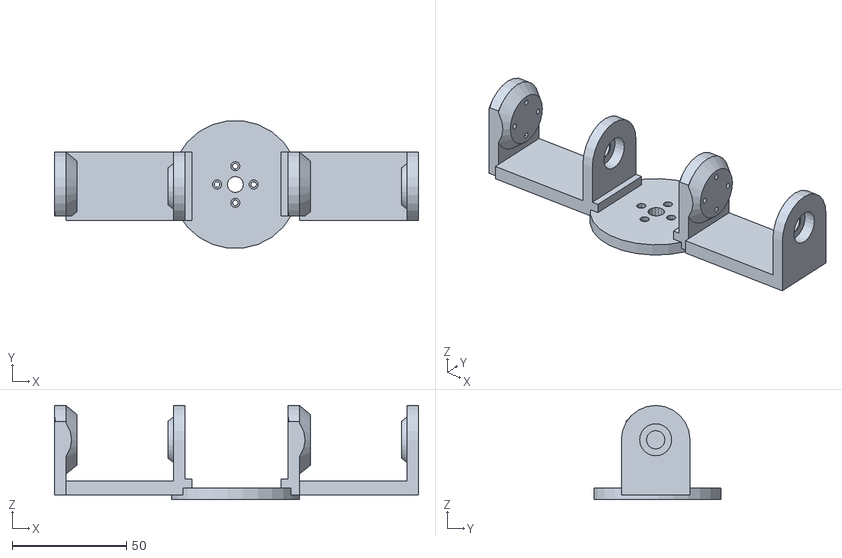
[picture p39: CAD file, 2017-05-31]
models/arm/gg_large_swl_base_v3.stl
159.0 x 55.6 x 41.1

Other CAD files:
models/arm/gg_upper_ef_v5.stl
models/arm/gg_tibia_v3.stl
models/arm/gg_femur_v3.stl

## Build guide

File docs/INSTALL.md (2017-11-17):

# Installation Instructions
1. Install OS (Jessie-Lite Sept) on three hosts.
    > **Note:** this demo has been built using Raspberry Pi 3 computers
1. Configure the three hosts to be on the same network and note each host's IP
1. On each host make a `~/mini-fulfillment` directory
1. Back on your development machine, execute the following steps.
    1. [Install](http://docs.aws.amazon.com/cli/latest/userguide/installing.html) 
    the AWS CLI and [configure](http://docs.aws.amazon.com/cli/latest/userguide/cli-chap-getting-started.html) 
    it with [Administrator](http://docs.aws.amazon.com/IAM/latest/UserGuide/getting-started_create-admin-group.html) 
    credentials.   
    1. Clone this git repo into a directory `~/aws-greengrass-mini-fulfillment/`
        - Example: `git clone https://github.com/awslabs/aws-greengrass-mini-fulfillment.git ~/aws-greengrass-mini-fulfillment`
        > **Note**: All subsequent instructions assume the developer's local copy of 
        this repository is in `~/aws-greengrass-mini-fulfillment/` if you chose 
        another directory, remember to take that into account throughout these 
        instructions. 
    1. From the top of the repository at `~/aws-greengrass-mini-fulfillment/`:
        - Install a virtual environment: `virtualenv venv --python=python2.7`
        - Activate the virtual environment: `source venv/bin/activate`
        - Execute: `pip install -r requirements.txt`
    1. [Create](http://docs.aws.amazon.com/iot/latest/developerguide/thing-registry.html) 
    the three Greengrass Core **things** and attach 
    [certificates](http://docs.aws.amazon.com/iot/latest/developerguide/managing-device-certs.html) 
    in AWS IoT. Specifically, to create the Greengrass Cores for this example:  
        ```bash
        cd ~/aws-greengrass-mini-fulfillment/groups
        ./group_setup.py create-core --thing-name sort_arm-core --config-file arm/sort_arm/cfg.json --cert-dir arm/sort_arm
        ./group_setup.py create-core --thing-name inv_arm-core --config-file arm/inv_arm/cfg.json --cert-dir arm/inv_arm
        ./group_setup.py create-core --thing-name master-core --config-file master/cfg.json --cert-dir master/certs
        ```
        > **Note:** You can see the details of each created Core recorded in the 
        `cfg.json` files used above in the `create-core` command. Example: 
        ```json
        {
          "core": {
            "cert_arn": "arn:aws:iot:us-west-2:EXAMPLE_ACCT:cert/EXAMPLE10bEXAMPLE34e3a3ac96f3903d040fcca1f7b6e83aba15d95a631622b",
            "cert_id": "EXAMPLE10bEXAMPLE34e3a3ac96f3903d040fcca1f7b6e83aba15d95a631622b",
            "thing_arn": "arn:aws:iot:us-west-2:EXAMPLE_ACCT:thing/sort_arm-core",
            "thing_name": "sort_arm-core"
          },...
        ``` 
    1. Download the `root-ca` file used by all three cores to communicate with 
    the AWS cloud. Then copy that `root-ca` to the proper directories:
        ```bash
        cd ~/aws-greengrass-mini-fulfillment/groups
        curl -o root-ca.pem https://www.symantec.com/content/en/us/enterprise/verisign/roots/VeriSign-Class%203-Public-Primary-Certification-Authority-G5.pem
        echo arm/sort_arm arm/sort_arm/ggd_certs | xargs -n 1 cp root-ca.pem
        echo arm/inv_arm arm/inv_arm/ggd_certs | xargs -n 1 cp root-ca.pem
        echo master/certs master/ggd/certs | xargs -n 1 cp root-ca.pem
        rm root-ca.pem
        ```
    1. Create the Greengrass Device **things** and **certificates** in AWS IoT 
        as follows:
        ```bash
        ./group_setup.py create-devices --thing-names '[sort_arm_ggd,sort_heartbeat_ggd]' --config-file arm/sort_arm/cfg.json --cert-dir arm/sort_arm/ggd_certs
        ./group_setup.py create-devices --thing-names '[inv_arm_ggd,inv_heartbeat_ggd]' --config-file arm/inv_arm/cfg.json --cert-dir arm/inv_arm/ggd_certs
        ./group_setup.py create-devices --thing-names '[button_ggd,belt_ggd,bridge_ggd,heartbeat_ggd,web_ggd]' --config-file master/cfg.json --cert-dir master/ggd/certs
        ./group_setup.py create-devices --thing-names '[master_brain]' --config-file master/cfg.json --cert-dir master/ggd/certs --append True --cloud_sync True
        ./group_setup.py associate-devices --thing-names '[inv_arm_ggd,sort_arm_ggd]' --config-file master/cfg.json
        ./group_setup.py associate-devices --thing-names '[bridge_ggd]' --config-file arm/sort_arm/cfg.json
        ./group_setup.py associate-devices --thing-names '[bridge_ggd]' --config-file arm/inv_arm/cfg.json
        ```
        > **Note:** You can see the details of each create Device recorded in the 
        `cfg.json` files used above in the `create-devices` command. Example:
        ```json
          ...
          "devices": {
            "sort_arm_ggd": {
              "cert_arn": "arn:aws:iot:us-west-2:EXAMPLE_ACCT:cert/EXAMPLEba1EXAMPLE32b63db0d3a830b7874dcb791cc045ad9bc7c64a058c87e",
              "cert_id": "EXAMPLEba1EXAMPLE32b63db0d3a830b7874dcb791cc045ad9bc7c64a058c87e",
              "thing_arn": "arn:aws:iot:us-west-2:EXAMPLE_ACCT:thing/sort_arm_ggd",
              "thing_name": "sort_arm_ggd"
            },...
        ```
    1. Create the Greengrass Group's Lambda functions
        ```bash
        ./lambda_setup.py create lambda/MasterBrain/cfg_lambda.json
        ./lambda_setup.py create lambda/MasterErrorDetector/cfg_lambda.json
        ./lambda_setup.py create lambda/ArmErrorDetector/cfg_lambda.json
        ```
    1. Associate the Lambda functions with the proper Greengrass Groups
        ```bash
        ./group_setup.py associate-lambda ./arm/sort_arm/cfg.json ./lambda/ArmErrorDetector/cfg_lambda.json
        ./group_setup.py associate-lambda ./arm/inv_arm/cfg.json ./lambda/ArmErrorDetector/cfg_lambda.json
        ./group_setup.py associate-lambda ./master/cfg.json ./lambda/MasterBrain/cfg_lambda.json
        ./group_setup.py associate-lambda ./master/cfg.json ./lambda/MasterErrorDetector/cfg_lambda.json
        ```
        > Note: You can see the details of each Lambda associated in the 
        `cfg.json` files. Example:
        ```json
          ...
          "lambda_functions": {
            "ArmErrorDetector": {
              "arn": "arn:aws:lambda:us-west-2:EXAMPLE_ACCT:function:ArmErrorDetector:mini",
              "arn_qualifier": "mini"
            }...
        ```
    1. Download and prep the servo software used by the Greengrass Devices
        ```bash
        ./servo_setup.py
        ```
    1. Instantiate the fully-formed Greengrass Groups with the following commands:
        ```bash
        ./group_setup.py create sort_arm ./arm/sort_arm/cfg.json --group-name sort_arm
        ./group_setup.py create inv_arm ./arm/inv_arm/cfg.json --group_name inv_arm
        ./group_setup.py create master ./master/cfg.json --group_name master
        ./group_setup.py deploy ./arm/sort_arm/cfg.json
        ./group_setup.py deploy ./arm/inv_arm/cfg.json
        ./group_setup.py deploy ./master/cfg.json
        ```
        > **Note:** until cross-group discovery is improved the `--group-name` options 
        above must be as written. The `bridge.py` Greengrass Device relies upon them
1. Prep the Greengrass software
    1. [Prepare](http://docs.aws.amazon.com/greengrass/latest/developerguide/prepare-raspi.html) each host for Greengrass  
    1. Go [here](https://us-west-2.console.aws.amazon.com/iotv2/home?region=us-west-2#/software/greengrass) 
       in the AWS console and download the `greengrass-linux-armv7` distribution
    1. Perform the **Installing the AWS Greengrass Core** [step](http://docs.aws.amazon.com/greengrass/latest/developerguide/gg-tutorial-rpi.html#gg-tutorial-rpi-provision-ggc)
1. Now copy the directories from the developer local `aws-greengrass-mini-fulfillment` repository 
   to each of the three Raspberry Pi hosts. Specifically, all contents of:
    - `~/aws-greengrass-mini-fulfillment/groups/arm` to `sort_arm-pi$ ~/mini-fulfillment/groups/arm`
    - `~/aws-greengrass-mini-fulfillment/groups/arm` to `inv_arm-pi$ ~/mini-fulfillment/groups/arm`, and
    - `~/aws-greengrass-mini-fulfillment/groups/master` to `master-pi$ ~/mini-fulfillment/groups/master`
1. On the `master` host
    1. `cd ~/mini-fulfillment/groups/master/`
    1. `pip install -r requirements.txt`
        > **Note** you might need to use `sudo` and it can take some time to 
        install `numpy`
    1. `chmod 755 cp_certs.sh servo_build.sh start_master.sh stop_master.sh`
    1. Make the Dynamixel SDK by executing `./servo_build.sh`
    1. Execute `./cp_certs.sh`. This will copy the host's certs into the 
       necessary GG Core location.
    1. As described in the **Configure AWS Greengrass Core** [step](http://docs.aws.amazon.com/greengrass/latest/developerguide/gg-tutorial-rpi.html#gg-tutorial-rpi-connect), edit the 
    configuration `/greengrass/config/config.json` as follows:
        ```json
        {
           "coreThing": {
               "caPath": "root-ca.pem",
               "certPath": "master-core.pem",
               "keyPath": "master-core.prv",
               "thingArn": "arn:aws:iot:[AWS_REGION_HERE]:[AWS_ACCOUNT_ID]:thing/master-core",
               "iotHost": "[HOST_PREFIX_HERE].iot.[AWS_REGION_HERE].amazonaws.com",
               "ggHost": "greengrass.iot.[AWS_REGION_HERE].amazonaws.com",
               "keepAlive": 600
           },
           "runtime": {
               "cgroup": {
                   "useSystemd": "yes"
               }
           }
        }
        ```
        > **Note:** determine the `thingArn` from the `~/mini-fulfillment/groups/master/cfg.json` 
        file on the host, determine the `iotHost` from the [Settings](https://us-west-2.console.aws.amazon.com/iotv2/home?region=us-west-2#/settings)
        in the IoT Console, and the `ggHost` AWS region will be the same as in the `thingArn` value.
1. On the `sort_arm` host
    1. `cd ~/mini-fulfillment/groups/arm/`
    1. `pip install -r requirements.txt`
        > **Note** you might need to use `sudo`
    1. `chmod 755 cp_sort_arm_certs.sh servo_build.sh start_sort_arm.sh stop_arm.sh`
    1. Make the Dynamixel SDK by executing `./servo_build.sh`
    1. Execute `./cp_sort_arm_certs.sh`. This will copy the host's certs into the 
       necessary GG Core location.
    1. As described in the **Configure AWS Greengrass Core** [step](http://docs.aws.amazon.com/greengrass/latest/developerguide/gg-tutorial-rpi.html#gg-tutorial-rpi-connect), edit the 
    configuration `/greengrass/config/config.json` as follows:
        ```json
        {
           "coreThing": {
               "caPath": "root-ca.pem",
               "certPath": "sort_arm-core.pem",
               "keyPath": "sort_arm-core.prv",
               "thingArn": "arn:aws:iot:[AWS_REGION_HERE]:[AWS_ACCOUNT_ID]:thing/sort_arm-core",
               "iotHost": "[HOST_PREFIX_HERE].iot.[AWS_REGION_HERE].amazonaws.com",
               "ggHost": "greengrass.iot.[AWS_REGION_HERE].amazonaws.com",
               "keepAlive": 600
           },
           "runtime": {
               "cgroup": {
                   "useSystemd": "yes"
               }
           }
        }
        ```
        > **Note:** determine the `thingArn` from the `~/mini-fulfillment/groups/arm/sort_arm/cfg.json` 
        file on the host, determine the `iotHost` from the [Settings](https://us-west-2.console.aws.amazon.com/iotv2/home?region=us-west-2#/settings) 
        in the IoT Console, and the `ggHost` AWS region will be the same as in the `thingArn` value.
1. On the `inv_arm` host
    1. `cd ~/mini-fulfillment/groups/arm/`
    1. `pip install -r requirements.txt` 
        > **Note** you might need to use `sudo`
    1. `chmod 755 cp_inv_arm_certs.sh servo_build.sh start_inv_arm.sh stop_arm.sh`
    1. Make the Dynamixel SDK by executing `./servo_build.sh`
    1. Execute `./cp_inv_arm_certs.sh`. This will copy the host's certs into the 
       necessary GG Core location.
    1. As described in the **Configure AWS Greengrass Core** [step](http://docs.aws.amazon.com/greengrass/latest/developerguide/gg-tutorial-rpi.html#gg-tutorial-rpi-connect), edit the 
    configuration `/greengrass/config/config.json` as follows:
        ```json
        {
           "coreThing": {
               "caPath": "root-ca.pem",
               "certPath": "inv_arm-core.pem",
               "keyPath": "inv_arm-core.prv",
               "thingArn": "arn:aws:iot:[AWS_REGION_HERE]:[AWS_ACCOUNT_ID]:thing/inv_arm-core",
               "iotHost": "[HOST_PREFIX_HERE].iot.[AWS_REGION_HERE].amazonaws.com",
               "ggHost": "greengrass.iot.[AWS_REGION_HERE].amazonaws.com",
               "keepAlive": 600
           },
           "runtime": {
               "cgroup": {
                   "useSystemd": "yes"
               }
           }
        }
        ```
        > **Note:** determine the `thingArn` from the `~/mini-fulfillment/groups/arm/inv_arm/cfg.json` 
        file on the host and determine the `iotHost` from the [Settings](https://us-west-2.console.aws.amazon.com/iotv2/home?region=us-west-2#/settings) 
        in the IoT Console, and the `ggHost` AWS region will be the same as in the `thingArn` value.
1. Using [the operation instructions](OPERATE.md) start the GG Cores and Devices in the following order:
    1. Start the `master` GG Core
    1. Start the `sort_arm` GG Core and the `sort_arm` GG Devices
    1. Start the `inv_arm` GG Core and the `inv_arm` GG Devices
    1. Start the `master` GG Devices
    
    :white_check_mark: at this point in time you should see the `master` host button box's white button light turn on.
1. Use the physical **`green`** and **` red`** buttons to **start** and **stop** the demo, respectively.
> **Note:** If you experience trouble, checkout the [troubleshooting](TROUBLE.md) doc

##### Instantiation of Greengrass Groups is now complete

`-=-=-=-=-`

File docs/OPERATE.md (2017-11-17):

## Operating the Mini Fulfillment center example
### Preparation
From your development machine open two command line terminals per host, for a 
total of six. The following instructions assume you have open and connected:
* `master-pi` terminal
* `sort_arm-pi` terminal
* `inv_arm-pi` terminal

### To start device operations of the Master host `master-pi`
1. **Start GG Core** -- in the `master-pi` terminal execute:
    ```bash
    cd /greengrass/ggc/packages/<version> 
    sudo ./greengrassd start
    ```
1. **Start GG Devices** -- in the `master-pi` terminal execute:
    ```bash
    cd ~/mini-fulfillment/groups/master
    ./start_master.sh
    ```
    > **Note:** you should see the white button light turn on, if connected.

After starting the master devices, to determine success you should see four 
entries in the list of processes, similar to the following:
```
master-pi$ screen -ls
There are screens on:
	8281.web	(11/19/2016 05:53:42 PM)	(Detached)
	8278.heartbeat	(11/19/2016 05:53:42 PM)	(Detached)
	8275.button	(11/19/2016 05:53:42 PM)	(Detached)
	8269.belt	(11/19/2016 05:53:42 PM)	(Detached)
4 Sockets in /var/run/screen/S-pi.
```
To view the output of any of the Greengrass Devices attach to the 
`screen` by using the command `screen -r <pid>`. Example that 
re-attaches to the `web` device process in the above list:
```
screen -r 8281
```
:warning: Remember to detach from the screen using `Ctrl-A, D` **not** `Ctrl-C`. 
Using `Ctrl-C` will exit the process being viewed.

If the `button` device started successfully the physical button lights will turn on.
If the `belt` device started successfully you'll see `[btt.__init__] frequency:<value>` 
in the output.

### To stop device operations of the Master host
1. **Stop GG Devices** -- in `master-pi` Terminal execute:
    ```bash
    cd ~/mini-fulfillment/groups/master
    ./stop_master.sh
    ```

### To start device operations of Arm host `sort_arm-pi`
1. **Start GG Core** -- in the `sort_arm-pi` Terminal execute:
    ```bash
    cd /greengrass/ggc/packages/<version> 
    sudo ./greengrassd start
    ```
1. **Start GG Devices** in the `sort_arm-pi` Terminal execute:
    ```bash
    cd ~/mini-fulfillment/groups/arm
    ./start_sort_arm.sh
    ```

After starting the arm, to determine success you should see two entries in the 
list of processes, similar to the following:
```bash
$ screen -ls
There are screens on:
	4961.heartbeat	(19/11/16 18:10:51)	(Detached)
	4958.arm	(19/11/16 18:10:51)	(Detached)
2 Sockets in /var/run/screen/S-pi.
```
To view the output of any of the Greengrass Devices attach to the 
`screen` by using the command `screen -r <pid>`. For example, the following command 
attaches to the `arm` device process in the above list:
```bash
screen -r 4958
```
:warning: Remember to detach from the screen using `Ctrl-A, D` **not** `Ctrl-C`. 
Using `Ctrl-C` will exit the process being viewed.

### To start device operations of Arm host `inv_arm-pi`
1. **Start GG Core** -- in the `inv_arm-pi` Terminal execute:
    ```bash
    cd /greengrass/ggc/packages/<version> 
    sudo ./greengrassd start
    ``` 
1. **Start GG Devices** -- in the `inv_arm-pi` Terminal execute:
    ```bash
    cd ~/mini-fulfillment/groups/arm
    ./start_inv_arm.sh
    ```

After starting the arm, to determine success you should see two entries in the 
list of processes, similar to the following:
```
$ screen -ls
There are screens on:
	4961.heartbeat	(19/11/16 18:10:51)	(Detached)
	4958.arm	(19/11/16 18:10:51)	(Detached)
2 Sockets in /var/run/screen/S-pi.
```
To view the output of any of the Greengrass Devices attach to the 
`screen` by using the command `screen -r <pid>`. For example, the following command 
attaches to the `arm` device process in the above list:
```
screen -r 4958
```
:warning: Remember to detach from the screen using `Ctrl-A, D` **not** `Ctrl-C`. 
Using `Ctrl-C` will exit the process being viewed.

### To stop device operations of either Arm host
1. **Stop GG Devices** -- in the Arm's terminal, execute:
    ```bash
    cd ~/mini-fulfillment/groups/arm/
    ./stop_arm.sh
    ```

### To start overall example operations
Push the **`green`** button to start both robot arms and the conveyor belt.

### To stop overall example operations
Push the **`red`** button to stop. 

### Using the white toggle button
The **`white`** button is a manual override that interacts with the Master 
Greengrass Core's local shadow to reverse the current direction of the conveyor 
belt. During normal operation this button is unnecessary; however, this button 
can be useful when demonstrating interactivity with the mini fulfillment center.

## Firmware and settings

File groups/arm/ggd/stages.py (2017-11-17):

#!/usr/bin/env python

# Copyright 2017 Amazon.com, Inc. or its affiliates. All Rights Reserved.
#
# Licensed under the Apache License, Version 2.0 (the "License"). You may not
# use this file except in compliance with the License. A copy of the License is
# located at
#     http://aws.amazon.com/apache2.0/
#
# or in the "license" file accompanying this file. This file is distributed on
# an "AS IS" BASIS, WITHOUT WARRANTIES OR CONDITIONS OF ANY KIND, either
# express or implied. See the License for the specific language governing
# permissions and limitations under the License.

"""
This file dictates the specifics of the motion of the arms.

Additionally, this file contains an ArmStages object that is instantiated by the
Greengrass Arm device every time a new stage is to be processed. Additionally, 
this file contains a command-line supporting manual operation and tuning of an 
arm through one stage at a time.
 
Note: At this point in time, tuning of an arm requires modifications to the 
servo values contained in this file.
"""
import math
import time
import logging
import argparse
import threading
import numpy.ma as ma

from decimal import Decimal, ROUND_HALF_UP
from servo.servode import Servo, ServoGroup, ServoProtocol

from image_processor import ImageProcessor
from . import arm_servo_ids

log = logging.getLogger('stages')
handler = logging.StreamHandler()
formatter = logging.Formatter(
    '%(asctime)s|%(name)-8s|%(levelname)s: %(message)s')
handler.setFormatter(formatter)
log.addHandler(handler)
log.setLevel(logging.INFO)

HOME_BASE = 450  # servo value of the 'home' position of the base servo
HOME_STRAIGHT = 512  # servo value of the 'straight' position of the base servo
HOME_FEMUR_1 = 520  # value of the 'home' position of the first femur servo
HOME_FEMUR_2 = 520  # value of the 'home' position of the second femur servo
HOME_TIBIA = 420  # servo value of the 'home' position of the tibia
OPEN_EFFECTOR = 500  # servo value of the 'open' position of the end effector
GRAB_EFFECTOR = 290  # servo value of 'grab' position of the end effector
POSITION_MARGIN = 75  # how close does the servo need to get the goal position
NO_BOX_FOUND = {'x': None, 'y': None}
MIN_OBJECT_SIZE = 200  # smallest object to try to pickup
MAX_IMAGE_WIDTH = 96  # used for coordinate calculations and camera constraint
MAX_IMAGE_HEIGHT = 96  # used for coordinate calculations and camera constraint


def cart2polar(x, y, degrees=True):
    """
    Convert cartesian X and Y to polar RHO and THETA.
    :param x: x cartesian coordinate
    :param y: y cartesian coordinate
    :param degrees: True = return theta in degrees, False = return theta in
        radians. [default: True]
    :return: r, theta
    """
    rho = ma.sqrt(x ** 2 + y ** 2)
    theta = ma.arctan2(y, x)
    if degrees:
        theta *= (180 / math.pi)

    return rho, theta


def polar2cart(rho, theta):
    """
    Convert polar coordinates to cartesian coordinated.

    :param rho: polar rho coordinate
    :param theta: polar theta coordinate in degrees
    :return:
    """
    x = rho * ma.cos(theta)
    y = rho * ma.sin(theta)
    return x, y


def cartesian_goals(x, y):
    """
    Use a cartesian coordinate system to calculate goals from given X and Y
    values.

    :param x: x cartesian coordinate
    :param y: y cartesian coordinate
    :return: cartesian derived base, fibia, and tibia servo goal values
    """
    # Convert 2D X and Y into usable numbers
    two_d_y_as_float = float(y)
    two_d_y_as_percent = float(two_d_y_as_float / 100)
    two_d_x_as_float = float(x)
    two_d_x_as_percent = float(two_d_x_as_float / 100)
    # Base maths
    # A - Turn X into a percent
    # B - Multiply X against the total travel of ThreeD_Base
    # C - Take the MAX of ThreeD_Base + B
    three_d_base_max = 780  # Then pad it some (740 + another say 40)
    three_d_base_min = 328  # Then pad it some (288 - another say 40)
    three_d_base_travel = three_d_base_max - three_d_base_min
    bg = int(
        three_d_base_max - (three_d_base_travel * two_d_x_as_percent)) - 60
    logging.info("[cartesian_goals] Base goal position is:{0}".format(bg))
    # Femur maths
    # A - Turn Y into a percent
    # B - Multiply Y against the total travel of ThreeD_Base
    # C - Take the MAX of ThreeD_Elbow - B
    three_d_femur_max = 451  # Then pad it some (550 + another say 40)
    three_d_femur_min = 363  # Then pad it some (420 - another say 40)
    three_d_femur_travel = three_d_femur_max - three_d_femur_min
    fg = int(
        three_d_femur_max - (three_d_femur_travel * two_d_y_as_percent))
    logging.info("[cartesian_goals] Femur goal position is:{0}".format(fg))
    # Tibia maths
    # A - Turn X into a percent
    # B - Multiply X against the total travel of threeD_femur
    # C - Take the MAX of threeD_Elbow + B
    three_d_tibia_max = 420  # Then pad it some (370 + another say 40)
    three_d_tibia_min = 150  # Then pad it some (135 - another say 40)
    three_d_tibia_travel = three_d_tibia_max - three_d_tibia_min
    tg = int(
        three_d_tibia_min + (three_d_tibia_travel * two_d_y_as_percent))
    logging.info("[cartesian_goals] Tibia goal position is:{0}".format(tg))
    return bg, fg, tg


def polar_goals(x, y):
    """
    Use a polar coordinate system to calculate goals from given X and Y
    values.

    :param x: x cartesian coordinate
    :param y: y cartesian coordinate
    :return: polar coordinate derived base, fibia, and tibia servo goal values
    """
    if y < 0:
        raise ValueError("Cannot accept negative Y values.")

    # base servo value which represents 0 degrees. Strongly dependent upon
    # physical construction, servo installation and location of arm
    polar_axis = 210
    polar_180_deg = 810  # base servo value which represents 180 degrees
    polar_diff = polar_180_deg - polar_axis

    x_shift = Decimal(MAX_IMAGE_WIDTH / 2).quantize(
        exp=Decimal('1.0'), rounding=ROUND_HALF_UP)
    log.info("[polar_goals] x_shift:{0}".format(x_shift))
    # shift origin of x, y to center of base
    shifted_x = x - x_shift
    log.info("[polar_goals] new_x:{0} new_y:{1}".format(shifted_x, y))

    # horizontal kicker to overcome what we think is image parallax
    if 40 < abs(shifted_x) < 10:
        shifted_x *= 1.25
    elif 90 < abs(shifted_x) < 40:
        shifted_x *= 1.40

    # convert shifted x and y to rho and theta
    rho, theta = cart2polar(int(shifted_x), int(y))
    log.info("[polar_goals] r:{0} theta:{1}".format(rho, theta))

    # convert theta into base rotation goal
    bg = int((polar_diff / 180) * theta + polar_axis)
    # ensure base goal does not go beyond the 180 or 0 servo rotation boundaries
    if bg > polar_180_deg:
        bg = polar_180_deg
    if bg < polar_axis:
        bg = polar_axis

    bg_cart, fg, tg = cartesian_goals(x, y)
    # Return polar coordinates for base and cartesian for arm goals. We found
    # this combination to work best through experimentation over hours of
    # operation.
    return bg + 20, fg, tg


class ArmStages(object):
    def __init__(self, servo_group):
        super(ArmStages, self).__init__()
        self.sg = servo_group

    def stage_stop(self):
        log.info("[stage_stop] _begin_")

        self.sg.goal_position([
            512,  # first servo value
            500,  # second servo value
            500,  # third servo value
            135,  # fourth servo value
            OPEN_EFFECTOR  # fifth servo value
        ], block=True, margin=POSITION_MARGIN)

        # add little sleepy motion in end effector for fun
        self.sg['effector']['goal_position'] = GRAB_EFFECTOR
        time.sleep(0.4)
        self.sg['effector']['goal_position'] = GRAB_EFFECTOR + 100
        time.sleep(0.4)
        self.sg['effector']['goal_position'] = GRAB_EFFECTOR
        time.sleep(0.4)
        self.sg['effector']['goal_position'] = GRAB_EFFECTOR + 30
        time.sleep(0.4)
        self.sg['effector']['goal_position'] = GRAB_EFFECTOR

        log.info("[stage_stop] _end_")

    def stage_home(self, should_run=None):
        """
        The arm will go to the ready position.

        :param should_run: a `threading.Event` that tells the stage to continue
            if `is_set()` is True
        :return: a dict containing this stage's results
        """
        log.info("[stage_home] _begin_")
        stage_results = dict()
        if len(self.sg) is not 5:
            log.error("[stage_home] Unexpected sg length:{0}".format(
                len(self.sg)))
            return stage_results

        # start at the middle-out position for all servos
        self.sg.goal_position([
            HOME_BASE,  # first servo value
            HOME_FEMUR_1,  # second servo value
            HOME_FEMUR_2,  # third servo value
            HOME_TIBIA,  # fourth servo value
            OPEN_EFFECTOR  # fifth servo value
        ], block=True, margin=POSITION_MARGIN)

        stage_results['reached_home'] = True
        log.info("[stage_home] _end_")
        return stage_results

    def stage_find(self, should_run=None):
        """
        The arm is actively using the end-effector camera to find objects of the
        correct size.

        :param should_run: a `threading.Event` that tells the stage to continue
            if `is_set()` is True
        :return: a dict containing this stage's results
        """
        log.info("[stage_find] _begin_")
        r = dict()

        ip = ImageProcessor(res_width=MAX_IMAGE_WIDTH,
                            res_height=MAX_IMAGE_HEIGHT)
        ip.capture_frame()

        log.info('[stage_find] max_pixel_count is:{0}'.format(
            ip.max_pixel_count))
        # check to see if the image processor found an object that is larger
        # than the minimum object size we want to try to pickup
        if ip.max_pixel_count > MIN_OBJECT_SIZE:
            print('largest object is:{0}'.format(ip.largest_object_id))
            print('largest object X coord is:{0}'.format(ip.largest_X))
            print('largest object Y coord is:{0}'.format(ip.largest_Y))
            r['x'] = ip.largest_X
            r['y'] = ip.largest_Y
            r['filename'] = ip.filename
            log.info("[stage_find] found object at x:{0} y:{1}".format(
                r['x'], r['y']))
            ip.close()
            log.info("[stage_find] _end_")
            return r
        else:
            # did not find an object larger than the minimum size - return
            # NO_BOX_FOUND
            log.info("[stage_find] no object larger than:{0}".format(
                MIN_OBJECT_SIZE))
            ip.close()
            log.info("[stage_find] _end_")
            return NO_BOX_FOUND

    def stage_pick(self, should_run=None,
                   cli=None, previous_results=None, cartesian=True):
        """
        The arm has found an object and will attempt to pick-up that object.

        :param should_run: a `threading.Event` that tells the stage to continue
            if `is_set()` is True
        :param cli: the cli values to use for the pick
        :param previous_results: a dict containing previous stage results
            pertinent to this stage
        :param cartesian: use cartesian (True) or polar coordinates (False) for
            the pick
        :return: a dict containing this stage's results
        """
        log.info("[stage_pick] _begin_")

        stage_results = dict()
        x = y = 0

        # if value is received from the CLI, use that as pickup goal target
        if cli is not None:
            x = cli.x
            y = cli.y
            if cli.polar is not None and cli.polar:
                cartesian = False

        # if value is received from previous results, use as pickup goal target
        if previous_results is not None:
            x = previous_results['x']
            y = previous_results['y']

        if cartesian:
            # use cartesian coordinates to calculate goals
            log.info("[stage_pick] x:{0} y:{1} cartesian pickup".format(x, y))
            base_goal, femur_goal, tibia_goal = cartesian_goals(x, y)
            log.info("[stage_pick] cart base:{0} femur:{1} tibia:{2}".format(
                base_goal, femur_goal, tibia_goal))
        else:
            # use polar coordinates to calculate goals
            log.info("[stage_pick] x:{0} y:{1} polar pickup".format(x, y))
            base_goal, femur_goal, tibia_goal = polar_goals(x, y)
            log.info(
                "[stage_pick] polar base:{0} femur:{1} tibia:{2}".format(
                    base_goal, femur_goal, tibia_goal))

        # ensure there are the expected number of servos in the ServoGroup
        if len(self.sg) is not 5:
            log.error("[stage_pick] Unexpected sg length:{0}".format(
                len(self.sg)))
            return stage_results

        # OPEN EFFECTOR/CLAW
        #####################################################
        self.sg.goal_position([
            HOME_BASE,
            HOME_FEMUR_1,
            HOME_FEMUR_2,
            HOME_TIBIA,
            OPEN_EFFECTOR
        ], block=False, margin=POSITION_MARGIN)
        time.sleep(.5)

        # go to PICK READY location
        ######################################################
        self.sg.goal_position([
            base_goal,
            HOME_FEMUR_1,
            HOME_FEMUR_2,
            HOME_TIBIA,
            OPEN_EFFECTOR
        ], block=False, margin=POSITION_MARGIN)
        time.sleep(.5)

        self.sg.write_values("moving_speed", [140, 140, 140, 140, 140])
        stage_results['slow_down'] = True

        # go to down-most open PICK location
        ######################################################
        self.sg.goal_position([
            base_goal,
            femur_goal,
            femur_goal,
            tibia_goal,
            OPEN_EFFECTOR
        ], block=False, margin=POSITION_MARGIN)
        time.sleep(.5)

        # change effector to the GRAB location
        ######################################################
        self.sg['effector']['goal_position'] = GRAB_EFFECTOR
        time.sleep(.5)

        # TODO: ensure something has been grabbed using torque feedback

        # the pick-up is now complete
        stage_results['pick_complete'] = True
        log.info("[stage_pick] _end_")

        return stage_results

    def stage_sort(self, should_run=None):
        """
        The arm has grabbed an object and will place that object at the sort
        position.

        :param should_run: a `threading.Event` that tells the stage to continue
            if `is_set()` is True
        :return: a dict containing this stage's results
        """
        log.info("[stage_sort] _begin_")
        stage_results = dict()

        sort_base = 512
        sort_femur_1 = 280
        sort_femur_2 = 280
        sort_tibia = 675

        # ensure there are the expected number of servos in the ServoGroup
        if len(self.sg) is not 5:
            log.error("[stage_sort] Unexpected sg length:{0}".format(
                len(self.sg)))
            return stage_results

        # slow down the move speed of all servos to reduce dropped objects
        ######################################################
        self.sg.write_values("moving_speed", [150, 150, 150, 150, 150])
        stage_results['slow_down'] = True

        # go to SORT "high" location
        ######################################################
        self.sg.goal_position([
            sort_base,  # first servo value
            HOME_FEMUR_1,  # second servo value
            HOME_FEMUR_2,  # third servo value
            sort_tibia,  # fourth servo value
            GRAB_EFFECTOR  # fifth servo value
        ], block=False, margin=POSITION_MARGIN)
        time.sleep(0.5)
        stage_results['raise_complete'] = True

        # go to SORT "extended" location
        ######################################################
        self.sg.goal_position([
            sort_base,  # first servo value
            sort_femur_1,  # second servo value
            sort_femur_2,  # third servo value
            sort_tibia,  # fourth servo value
            GRAB_EFFECTOR  # fifth servo value
        ], block=True, margin=POSITION_MARGIN + 15)
        time.sleep(0.5)
        stage_results['reach_complete'] = True

        # open the end effector/claw to drop object
        ######################################################
        self.sg['effector']['goal_position'] = OPEN_EFFECTOR
        time.sleep(0.5)

        # go to SORT "away" location
        ######################################################
        self.sg.goal_position([
            sort_base,  # first servo value
            sort_femur_1 + 150,  # second servo value
            sort_femur_2 + 150,  # third servo value
            HOME_TIBIA,  # fourth servo value
            OPEN_EFFECTOR  # fifth servo value
        ], block=False, margin=POSITION_MARGIN)

        # increase move speed of all servos to normal
        ######################################################
        self.sg.write_values("moving_speed", [200, 200, 200, 200, 200])
        stage_results['slow_down'] = False

        # the sort stage is now complete
        stage_results['sort_complete'] = True
        log.info("[stage_sort] _end_")
        return stage_results


def all_stages(servo_group, should_run, cli=None, previous_results=None):
    arm_stage = ArmStages(servo_group=servo_group)
    home_res = arm_stage.stage_home(should_run=should_run)
    find_res = arm_stage.stage_find(should_run=should_run)
    pick_res = arm_stage.stage_pick(should_run=should_run,
                                    cli=cli, previous_results=find_res)


def cli_home(servo_group, should_run, cli=None, previous_results=None):
    arm_stage = ArmStages(servo_group=servo_group)
    arm_stage.stage_home(should_run)


def cli_find(servo_group, should_run, cli=None, previous_results=None):
    arm_stage = ArmStages(servo_group=servo_group)
    arm_stage.stage_find(should_run)


def cli_pick(servo_group, should_run, cli=None, previous_results=None):
    arm_stage = ArmStages(servo_group=servo_group)
    arm_stage.stage_pick(should_run, cli, previous_results)


def cli_sort(servo_group, should_run, cli=None, previous_results=None):
    arm_stage = ArmStages(servo_group=servo_group)
    arm_stage.stage_sort(should_run)


def cli_stop(servo_group, should_run, cli=None, previous_results=None):
    arm_stage = ArmStages(servo_group=servo_group)
    arm_stage.stage_stop()


if __name__ == '__main__':
    parser = argparse.ArgumentParser(
        description='Mini Fulfillment Arm stages - command line interface',
        formatter_class=argparse.ArgumentDefaultsHelpFormatter)
    subparsers = parser.add_subparsers()

    home_parser = subparsers.add_parser(
        'home',
        description='Tell arm to move to HOME position.')
    home_parser.set_defaults(func=cli_home)

    find_parser = subparsers.add_parser(
        'find',
        description='Tell arm to FIND a box.'
    )
    find_parser.set_defaults(func=cli_find)

    pick_parser = subparsers.add_parser(
        'pick',
        description='Tell arm to PICKup a box.'
    )
    pick_parser.add_argument('x', default=0, nargs='?', type=int,
                             help="The 'X' coordinate to pickup a box.")
    pick_parser.add_argument('y', default=0, nargs='?', type=int,
                             help="The 'Y' coordinate to pickup a box.")
    pick_parser.add_argument('--polar', action='store_true',
                             help="Use polar coordinates to pickup a box.")
    pick_parser.set_defaults(func=cli_pick)

    sort_parser = subparsers.add_parser(
        'sort',
        description='Tell arm to SORT a box.'
    )
    sort_parser.set_defaults(func=cli_sort)

    args = parser.parse_args()

    with ServoProtocol() as sp:
        sg = ServoGroup()
        sg['base'] = Servo(sp, arm_servo_ids[0])
        sg['femur01'] = Servo(sp, arm_servo_ids[1])
        sg['femur02'] = Servo(sp, arm_servo_ids[2])
        sg['tibia'] = Servo(sp, arm_servo_ids[3])
        sg['effector'] = Servo(sp, arm_servo_ids[4])

        event = threading.Event()
        event.set()
        res = args.func(sg, event, args)
        print("Stage: {0} result: {1}".format(args.func, res))

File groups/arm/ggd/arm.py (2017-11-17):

#!/usr/bin/env python

# Copyright 2017 Amazon.com, Inc. or its affiliates. All Rights Reserved.
#
# Licensed under the Apache License, Version 2.0 (the "License"). You may not
# use this file except in compliance with the License. A copy of the License is
# located at
#     http://aws.amazon.com/apache2.0/
#
# or in the "license" file accompanying this file. This file is distributed on
# an "AS IS" BASIS, WITHOUT WARRANTIES OR CONDITIONS OF ANY KIND, either
# express or implied. See the License for the specific language governing
# permissions and limitations under the License.

"""
Greengrass Arm device

This Greengrass device controls the mini-fulfillment center 3D printed robotic 
arm. It accomplishes this using two threads: one thread to control and report 
upon the arm's movement through `stages` and a separate thread to read and 
report upon each of the arm's servo telemetry. 

The control stages that the arm device will execute in order, are:
* `home` - the arm is in or has returned to the ready position
* `find` - the arm is actively using the end-effector camera to find objects of 
    the correct size
* `pick` - the arm has found an object and will attempt to pick-up that object
* `sort` - the arm has grabbed an object and will place that object at the sort 
    position

To act in a coordinated fashion with the other Group's in the 
miniature fulfillment center, this device also subscribes to device shadow in 
the Master Greengrass Group. The commands that are understood from the master 
shadow are:
* `run` - the arm will start executing the stages in order
* `stop` - the arm will cease operation and go to the stop position

This device expects to be launched form a command line. To learn more about that 
command line type: `python arm.py --help`
"""

import os
import json
import time
import requests
import logging
import argparse
import datetime
import threading
import collections
from cachetools import TTLCache
from requests import ConnectionError
from AWSIoTPythonSDK.MQTTLib import AWSIoTMQTTClient, AWSIoTMQTTShadowClient

from AWSIoTPythonSDK.core.greengrass.discovery.providers import \
    DiscoveryInfoProvider
from AWSIoTPythonSDK.MQTTLib import AWSIoTMQTTClient, DROP_OLDEST
import utils
from . import arm_servo_ids
from gg_group_setup import GroupConfigFile

from stages import ArmStages, NO_BOX_FOUND
from servo.servode import Servo, ServoProtocol, ServoGroup


dir_path = os.path.dirname(os.path.realpath(__file__))

log = logging.getLogger('arm')
handler = logging.StreamHandler()
formatter = logging.Formatter(
    '%(asctime)s|%(name)-8s|%(levelname)s: %(message)s')
handler.setFormatter(formatter)
log.addHandler(handler)
log.setLevel(logging.INFO)

commands = ['run', 'stop']

should_loop = True

ggd_name = 'Empty'
cmd_event = threading.Event()
cmd_event.clear()

base_servo_cache = TTLCache(maxsize=32, ttl=120)
femur01_servo_cache = TTLCache(maxsize=32, ttl=120)
femur02_servo_cache = TTLCache(maxsize=32, ttl=120)
tibia_servo_cache = TTLCache(maxsize=32, ttl=120)
eff_servo_cache = TTLCache(maxsize=32, ttl=120)


def shadow_mgr(payload, status, token):
    log.info("[shadow_mgr] shadow payload:{0} token:{1}".format(
        json.dumps(json.loads(payload), sort_keys=True), token))


def initialize(device_name, config_file, root_ca, certificate, private_key,
               group_ca_path):
    global ggd_name

    cfg = GroupConfigFile(config_file)
    local = dict()
    remote = dict()

    # determine heartbeat device's thing name and endpoint for MQTT clients
    ggd_name = cfg['devices'][device_name]['thing_name']
    iot_endpoint = cfg['misc']['iot_endpoint']

    # Discover Greengrass Core
    dip = DiscoveryInfoProvider()
    dip.configureEndpoint(iot_endpoint)
    dip.configureCredentials(
        caPath=root_ca, certPath=certificate, keyPath=private_key
    )
    dip.configureTimeout(10)  # 10 sec
    log.info("Discovery using CA: {0} certificate: {1} prv_key: {2}".format(
        root_ca, certificate, private_key
    ))
    # Now discover the groups in which this device is a member.
    # The arm should only be in two groups. The local and master groups.
    discovered, discovery_info = utils.ggc_discovery(
        ggd_name, dip, retry_count=10, max_groups=2
    )

    # Each group returned has a groupId which can compare to the configured
    # groupId in the config file. If the IDs match, the 'local' Group has been
    # found and therefore local core.
    # If the groupId's do not match, the 'remote' or 'master' group has been
    # found.
    group_list = discovery_info.getAllGroups()
    for g in group_list:
        logging.info("[initialize] group_id:{0}".format(g.groupId))
        if g.groupId == cfg['group']['id']:
            local_cores = g.coreConnectivityInfoList
            local['core'] = local_cores[0]  # just grab first core as local
            local['ca'] = g.caList
        else:
            remote_cores = g.coreConnectivityInfoList
            remote['core'] = remote_cores[0]  # just grab first core as remote
            remote['ca'] = g.caList

    if len(local) > 1 and len(remote) > 1:
        logging.info("[initialize] local_core:{0} remote_core:{1}".format(
            local, remote
        ))
    else:
        raise EnvironmentError("Couldn't find the arm's Cores.")

    # just save one of the group's CAs to use as a CA file later
    local_core_ca_file = utils.save_group_ca(
        local['ca'][0], group_ca_path, local['core'].groupId
    )
    remote_core_ca_file = utils.save_group_ca(
        remote['ca'][0], group_ca_path, remote['core'].groupId
    )

    # Greengrass Cores discovered, now connect to Cores from this Device
    # get a client to send telemetry
    local_mqttc = AWSIoTMQTTClient(ggd_name)
    log.info("[initialize] local gca_file:{0} cert:{1}".format(
        local_core_ca_file, certificate))
    local_mqttc.configureCredentials(
        local_core_ca_file, private_key, certificate
    )
    local_mqttc.configureOfflinePublishQueueing(10, DROP_OLDEST)

    if not utils.mqtt_connect(mqtt_client=local_mqttc, core_info=local['core']):
        raise EnvironmentError("Connection to GG Core MQTT failed.")

    # get a shadow client to receive commands
    master_shadow_client = AWSIoTMQTTShadowClient(ggd_name)
    log.info("[initialize] remote ca_file:{0} cert:{1}".format(
        local_core_ca_file, certificate))
    remote_mqttc = master_shadow_client.getMQTTConnection()
    remote_mqttc.configureCredentials(
        remote_core_ca_file, private_key, certificate
    )

    if not utils.mqtt_connect(mqtt_client=master_shadow_client,
                              core_info=remote['core']):
        raise EnvironmentError("Connection to Master Shadow failed.")
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

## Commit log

2017-05-31 initial models checkin
    [gg_aws_logo.stl, gg_base_v2-3.stl, gg_button_box.stl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]
2017-06-01 git subrepo clone --force https://github.com/brettf/servode.git groups/master/ggd/servode
    subrepo:
    subdir: "groups/master/ggd/servode"
    merged: "a010229"
    upstream:
    origin: "https://github.com/brettf/servode.git"
    branch: "master"
    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
2017-06-01 git subrepo clone --force https://github.com/brettf/servode.git groups/sort_arm/ggd/servode
    subdir: "groups/sort_arm/ggd/servode"
    commit: "a010229"
    git-subrepo:
    version: "0.3.1"
    origin: "https://github.com/ingydotnet/git-subrepo"
    commit: "a7ee886"
    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
2017-06-01 git subrepo clone --force https://github.com/brettf/servode.git groups/inv_arm/ggd/servode
    subdir: "groups/inv_arm/ggd/servode"
    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
2017-06-06 switched to aliased Lambdas
2017-06-06 reworked to use config file
    [belt.py]
2017-06-06 git subrepo pull groups/master/ggd/servode
    merged: "81bf358"
    commit: "bcb13bd"
    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
2017-06-06 reworking inclusion of servo caps
    [belt.py, hello_example.py, servode.py]
2017-06-06 git subrepo clone https://github.com/brettf/servode.git groups/master/ggd/servo/
    subdir: "groups/master/ggd/servo"
    merged: "767a117"
    commit: "767a117"
    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
2017-06-06 added master servo sub-repo
2017-06-06 git subrepo clone https://github.com/brettf/servode.git groups/inv_arm/ggd/servo/
    subdir: "groups/inv_arm/ggd/servo"
    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
2017-06-06 git subrepo clone https://github.com/brettf/servode.git groups/sort_arm/ggd/servo/
    subdir: "groups/sort_arm/ggd/servo"
    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
2017-06-06 updating servo location
2017-06-06 git subrepo pull groups/master/ggd/servo
    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
2017-06-06 git subrepo pull groups/inv_arm/ggd/servo
    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
2017-06-06 git subrepo pull groups/sort_arm/ggd/servo
    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
2017-06-06 git subrepo pull groups/sort_arm/ggd/servo
    merged: "28bda41"
    commit: "28bda41"
    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
2017-06-06 git subrepo pull groups/master/ggd/servo
    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
2017-06-06 git subrepo pull groups/inv_arm/ggd/servo
    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
2017-06-06 exception handling when bridge fails
    [bridge.py]
2017-06-06 bringing 'arm' up to date
2017-06-06 initial arm-specific requirements
2017-06-26 switched constructor
2017-07-03 switch to gg-group-setup
2017-07-03 consolidating arm code
2017-07-03 consolidated arm groups directory
2017-07-03 git subrepo clone git@github.com:brettf/servode.git groups/arm/ggd/servo
    subdir: "groups/arm/ggd/servo"
    origin: "git@github.com:brettf/servode.git"
    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
2017-07-03 git subrepo clone https://github.com/brettf/servode.git groups/arm/ggd/servo
    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
2017-07-05 consolidated arm structure
2017-07-05 revised for arm code consolidation
2017-07-06 updated with common arm dir
2017-07-06 fleshed out servo info
2017-07-07 adding in base-to-femur servo mount spacer
    [gg_base_turn_table.stl]
2017-09-12 bom and construction updates
2017-09-19 emphasize aligned servo lines
2017-09-28 added two specific arm GroupTypes otherwise GGD names would be wrong
2017-09-28 updated to reflect specific arm GroupTypes
2017-09-28 updated to reflect specific arm GGDs
2017-09-29 fixed cross group devices
2017-09-29 made device names variable
2017-09-29 cleaned and updated config for device checks
2017-10-24 belt with discovery
2017-10-25 load servo profile
2017-10-25 added in servode tidbit
2017-10-25 now servo 'ping' is first command
2017-10-25 discovery working on these belt and button
2017-11-03 added associate-devices instructions
2017-11-15 added command for creation of master_brain shadow device
2017-11-15 fixed dual discovery logic
    [arm.py]
2017-11-16 fixed 'box' mode for button device
